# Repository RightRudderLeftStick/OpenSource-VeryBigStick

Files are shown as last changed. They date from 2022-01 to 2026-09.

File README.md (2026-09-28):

# OPEN SOURCE VERY BIG STICK PROJECT 2026
A very large joystick gimbal for very big sticks and now pedals too!

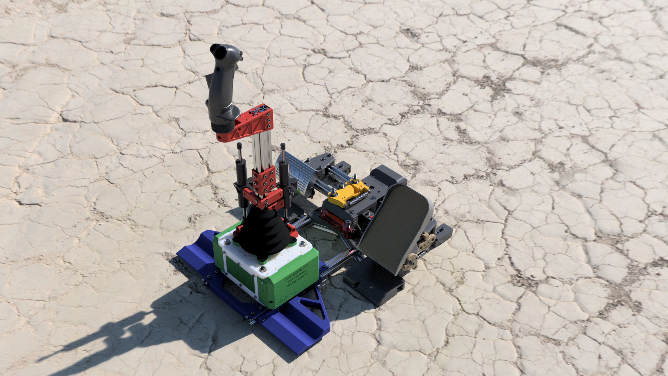
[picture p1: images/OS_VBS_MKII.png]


This totally open source gimbal is designed for end users to either connect existing Thrustmaster compatible grips or attach any custom grip directly to the base. It supports very high spring forces allowing for very realistic feeling flight controls.

It is recommended all parts are printed in PETG, while PLA+ may be acceptable for all parts other than the CAMS, which can be ordered from 3D printed providers in very durable materials.

Checkout the PDF file in the repo to see the bill of materials and the print orientation guide. 

## The current version is Beta 1.4.0

For printing CAMs, it is recommended for "jet" style flying with a full length extension (office chair height) to use "HARD_CAMS" and for medium length (seated low in a sim pit) to use "MED_CAMS". The use of "SOFT_CAMS" is only recommended for warbirds (WWII prop aircraft) or helicopters.

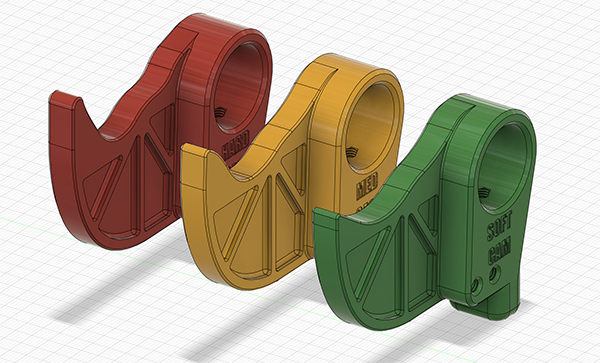
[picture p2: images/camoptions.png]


Check out this build guide below to learn how to assemble the base gimbal!

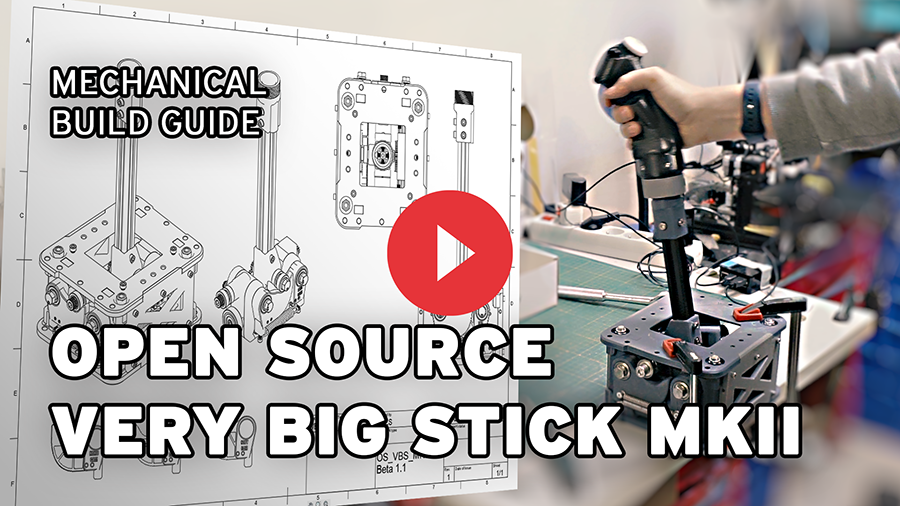
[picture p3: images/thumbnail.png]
Watch the video (https://www.youtube.com/watch?v=IdYbF5dOYag)


This video shows on to connect the electrical wiring and assemble the office chair mount.

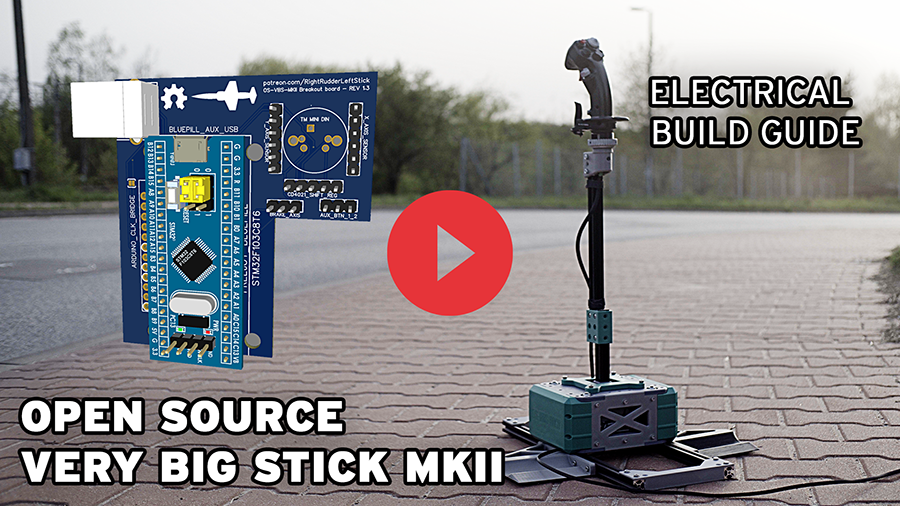
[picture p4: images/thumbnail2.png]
Watch the video (https://youtu.be/jo0v6YuI9vU)


## Patreon
Follow the progress at my patreon. Subscribers recieve early indevelopment F3D project files and other exclusive updates:

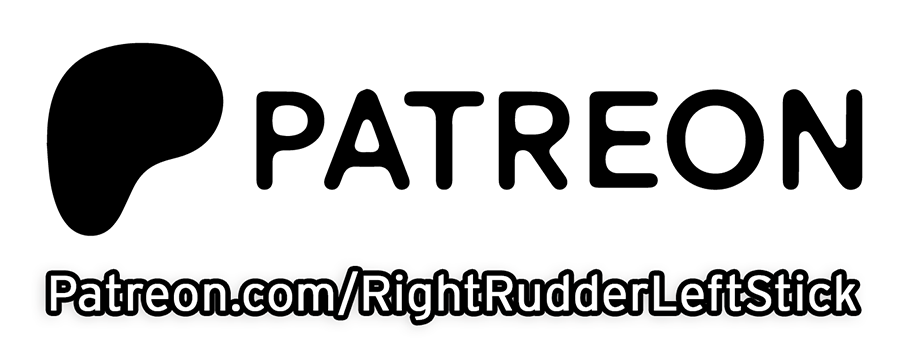
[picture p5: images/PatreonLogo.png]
Link to patreon (https://www.patreon.com/RightRudderLeftStick)


## PCBWAY

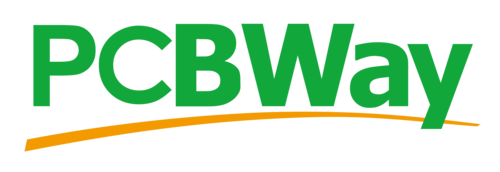
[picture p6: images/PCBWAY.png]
(https://pcbway.com/g/jks8J3)


You can also order the breakout PCB directly from PCBWAY, as well as the CAMs to print in Glass fibre Nylon for extra durability and higher quality than what can be done on most home printers.

### ORDER LINKS FOR PCBWAY
[PCB boards](https://www.pcbway.com/project/shareproject/Open_Source_Very_Large_Stick_Freejoy_MMjoy2_breakout_board_f66f472f.html)

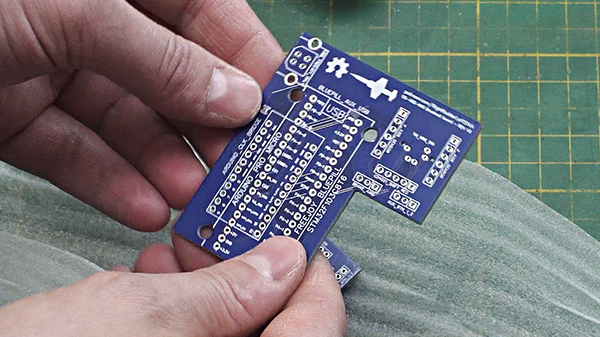
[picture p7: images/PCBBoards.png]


**CAMS** 
(4 are required for a complete set. Order in Glass Fibre Nylon)

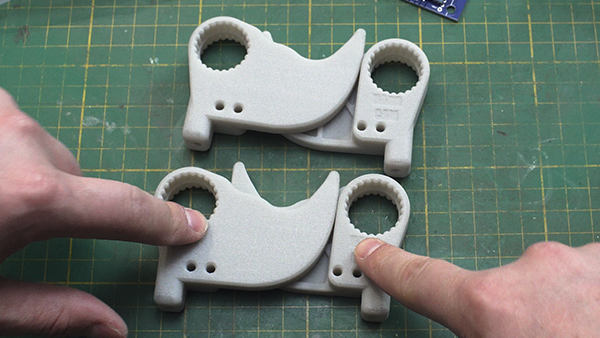
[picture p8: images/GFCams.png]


[Soft Cam](https://www.pcbway.com/project/shareproject/Open_Source_Very_Large_Stick_SOFT_CAM_c2835ecf.html)

[Medium Cam](https://www.pcbway.com/project/shareproject/Open_Source_Very_Large_Stick_MEDIUM_CAM_0f6965ab.html)

[Hard Cam](https://www.pcbway.com/project/shareproject/Open_Source_Very_Large_Stick_HARD_CAM_c53480e9.html)

## Partner Projects

### TheSimNet

Please Checkout TheSimNet's Youtube Channel. He releases designs of fully 3D printable flight grips with TM compatbility. All the renders of the OS-VBS-MK2 use his Free B-8 Grip models for reference. He also sells really cool projects like a very accurate F-15C grip. 

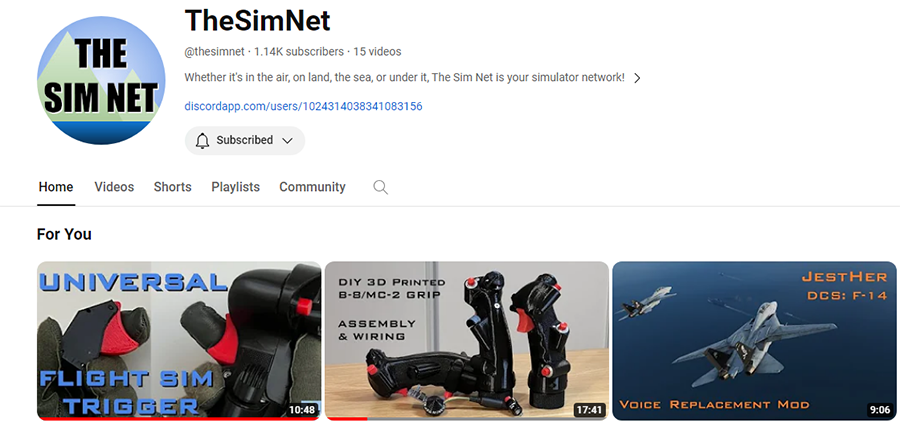
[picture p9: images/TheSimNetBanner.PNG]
Check out this channel (https://youtu.be/-zjJm-5tHko)


### Freejoy

Freejoy is an excellent open source alternative to MMjoy2 and is great for creating for really low cost and powerful USB game controller devices.... if you can still find genuine STM32 boards. 

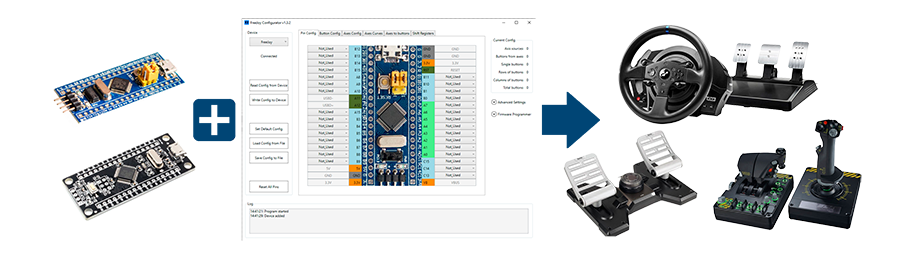
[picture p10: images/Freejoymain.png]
Check out this channel (https://github.com/FreeJoy-Team/FreeJoy)


Link to Freejoy [github.](https://github.com/FreeJoy-Team/FreeJoy)

# Changelog

### 1.4.2
- Added a version 2 of the AS5600 burner script

### 1.4.1
- Pedal stl  & step files now included!

### 1.4.0
- Added A5600 sensor support to the gimbal. New file called *AS5600_Sensor_Mount_vr3.stl* added which can hold the white breakout board sensor.
- Revised the parts *MainSleeve.stl, PitchFrame_PillowBlock.stl, RollFrame_PitchPin_Gear.stl, RollFrame_CamSide.stl & RollFrame_GearSide.stl* to update to the compliance holes from the pedal design
- *RollFrame_PitchPin_Gear.stl* now prints standing up for better support of the magnet slot.
- *PitchFrame_TopPlate.stl* has been revised with the latest patreon info and version code.
- Note the Analog pins on the AS5600 sensor should always be aligned to face the N on the magnet slot. This centers the 245 and 290 degree range thats burn with the script.
- *OuterCamCover_Solid.stl* updated with CLOS tier patreon backer credits.

### 1.3.8
- Added STM32 script for burning AS5600 sensor.

### 1.3.7
- Changed all the *.3mf files to *.stl files as there is an incompatbility with the 3mf generated by cura with orca/bambu slicer.

### 1.3.6
- Added a TPU_Boot.3mf which is a printable TPU cover to go over the top of the gimbal to keep dust and debris out of the mechanism. Print slowly as there are 60 degree overhangs in the design.

### 1.3.5
- Added the OuterCamCover_FreejoyUSB.3mf which has a port for the USB-B port when using freejoy to stick out. a regular USB cable connected directly to the bluepill or ardiuno can also go through this hole with a strain relief plate attached with M3 screws

### 1.3.4
- Added the sideplate.3mf. These just snap over the sides of the gimbal that are open to cover them.
- Added the authentikit Spade grip adapter, see community add-ons directory.
- Modified the wheel chocks and crossbar pieces to have 1.5mm of height from the floor. This raises the aluminum extrusions so the edges don't scratch hardwood floors. This also will be for heigh compatiblity with the rudder pedals which will also have the 1.5mm of space.

### 1.3.3
- Added the bushplane grip as an optional single button handle for the gimbal. included in the BushPlane_Grip directory.
- Added a new restrictor plate called "CYC_Split_RestrictorPlate_20degrees.3mf" that replaces the original 3mf of the restrictor plate. It comes in two parts and allows itself to be removed or replaced without diassembling the stick column

### 1.3.2a

- Fixed a net error in the PCBbreakout board (now revision 1.5) which required reordering the IO buttons on the breakout.

### 1.3.2

- Fixed an error in the breakout board where the TM mini DIN had the wrong pin orientation. 
- Fixed mislabelling on the USB breakout pins.
- Added 13 extra button IO pins to the breakout board. Now using freejoy a B-8 style grip can have all the buttons wired directly without using a shift register.

### 1.3.1

- Fixed the quantity in the build guide for "2020_Crossbar.3mf" from 1 to 2.

### 1.3

- Updated with electrical gerber files for the breakout board
- New TM adapter piece that has an offset for use with common chairs
- Revisions to several pieces, including a new "PitchFrame_TopPlate" that includes extra M5 holes for the future cyclic piston damper upgrade and cut outs to make it easier to fit a socket wrench into the gimbal to change cams
- Added Add-on for office chair mount
- Added the configuration file for MMJOY2
- Adjusted the PitchFrame_PillowBlock.3mf to have wider holes for feeding the wires through.
- Redesigned the CAMs to not require the Cam_Bearing_washer.3mf and to nicely friction fit the 608 bearings with compliance holes.

### 1.2
- Revised the TM adapter piece to have the clearance for the X shape at the bottom of the TM grip connector

### 1.1

- Fix to the TM adapter to add a second set of holes.

### 1.0

- Intial release of the mechanical parts of the gimbal, as seen in the mechanical guide video.

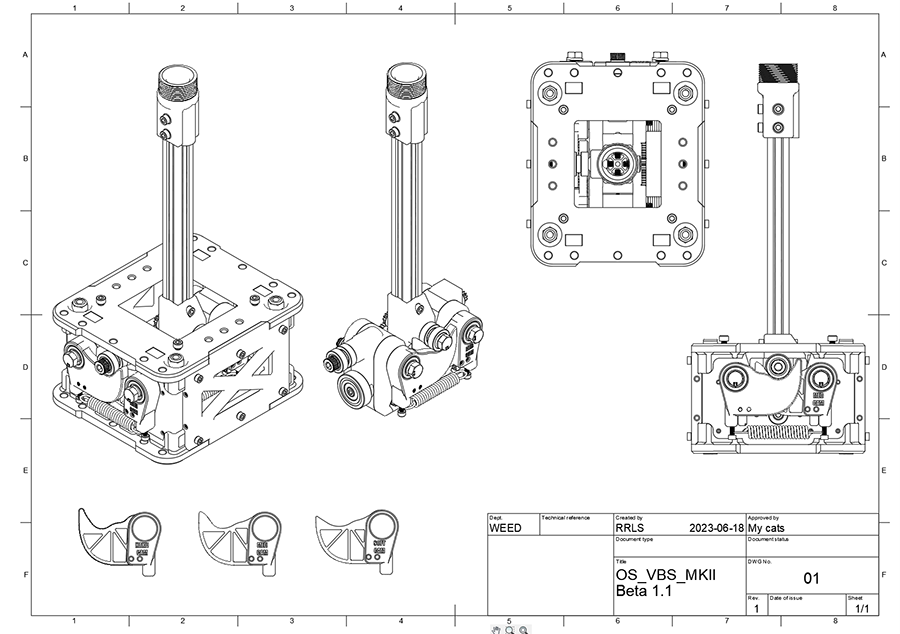
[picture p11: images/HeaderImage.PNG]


---



[This project is licensed as CC BY-SA 2.0](https://creativecommons.org/licenses/by-sa/2.0/)

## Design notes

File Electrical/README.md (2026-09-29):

# Firmware for microcontrollers

## Breakout Board

The breakout board is designed to socket either a STM32F103C8 microcontroller board (freejoy) or an Arduino Pro Micro (MMJOY2 or custom code). You can use the gerber file to order the PCB from your local assembler, or order directly from PCBWAY [here](https://www.pcbway.com/project/shareproject/Open_Source_Very_Large_Stick_Freejoy_MMjoy2_breakout_board_f66f472f.html).

Current Revision is 1.5

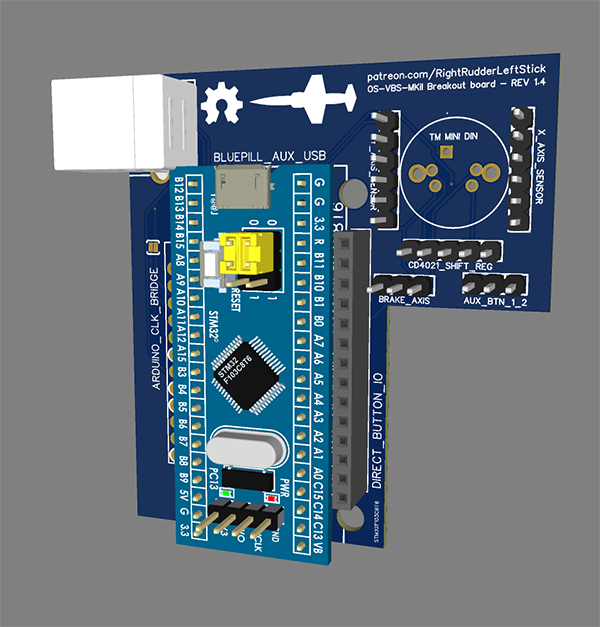
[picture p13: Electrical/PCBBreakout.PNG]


## MMJOY2 version

The MMJOY2 variation will require an Andruino Pro Micro, and the solder bridge must be connected on the PCB to set it for this configuration.

This is the public directory of all the version of MMJOY2 that were released before the project was halted.

Link to [website.](https://sites.google.com/site/mmjoyproject/%D1%84%D0%B0%D0%B9%D0%BB%D1%8B-%D0%B4%D0%BB%D1%8F-%D1%81%D0%BA%D0%B0%D1%87%D0%B8%D0%B2%D0%B0%D0%BD%D0%B8%D1%8F) 

For best reliabilty and compatibility with the included .mmjoy2 file. Use MMJOY2[v20160818upd1].rar

## Freejoy version

Using the freejoy version requires a **genuine** STM32F103C8 microcontroller board. Counterfeit STM32 chips cause all sorts of unpredictable problems with the Freejoy firmware. Try and order your STM32F103C8 from a trusted retailer with a proper return policy. 

Freejoy version requires a specialized firmware on top of v1.7.1_1b3 that is publically avaliable. Due to the length of the stick and wiring the timing of the CD4021 shift registers causes ghosting of inputs. This specialized firmware adjusts this. It is in the /Firmware/ directory.

In the /config/ directory there is also the w.i.p config file. It doesn't yet support the new IO pins of the 1.4 board revision.

Link to Freejoy [github.](https://github.com/FreeJoy-Team/FreeJoy)

## AS5600 Sensor Option

Because of supply chain issues, the EOL of the TLE5011 sensor, tariffs, some regions not having aliexpress, I've decided to support the very common AS5600 encoder sensor on the white breakout board. 

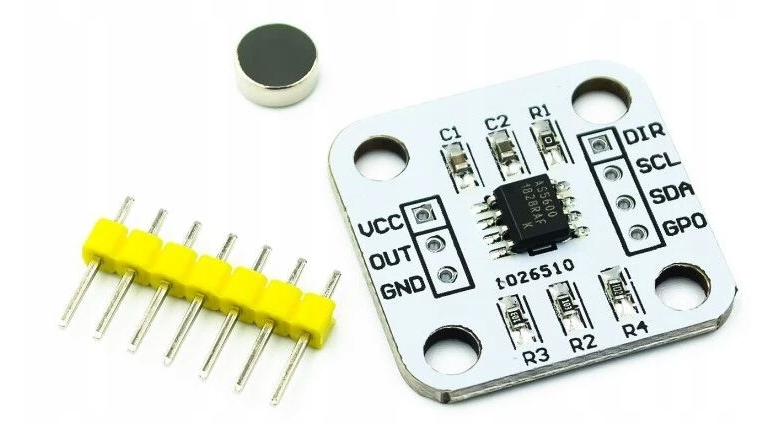
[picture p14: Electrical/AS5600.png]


The AS5600 is extremely common, as its used as an encoder on motors. The problem is its range is a full 360 degrees, which means for the 37 degrees we actually use that's only 440 steps of sensitivity over the range, which is reduced even more if you have a noisy signal.

I've created a script that can run on the bluepill before flashing freejoy that uses the internal chip register to instead convert the 360 range to a much narrower 50 degrees. This is a permanent "burn" operation into the chips memory. What it does is take the 360 degree range and truncate it to 245 - 290 degrees, which now will respond with 0-3.3v over the analog out, massively improving the sensors sensitivity. What this means is mounting the small magnet is extremely important to get within 10 degrees of north orientation, as we have 50 degrees to fit the 37 degrees of actual axis movement.

Here is the pin out guide to setting up the ship programmer.

BLUEPILL | 3.3v | GND | B6 | B7 | 
--- | --- | --- | --- | --- |
AS5600  | VCC | GND | SCL | SDA |

You load the [STM32_AS5600_Burner.bin](https://github.com/RightRudderLeftStick/OpenSource-VeryBigStick/tree/main/Electrical/As5600%20Sensor) with the ST-link utility just like how you flash the freejoy firmware for the first time. 

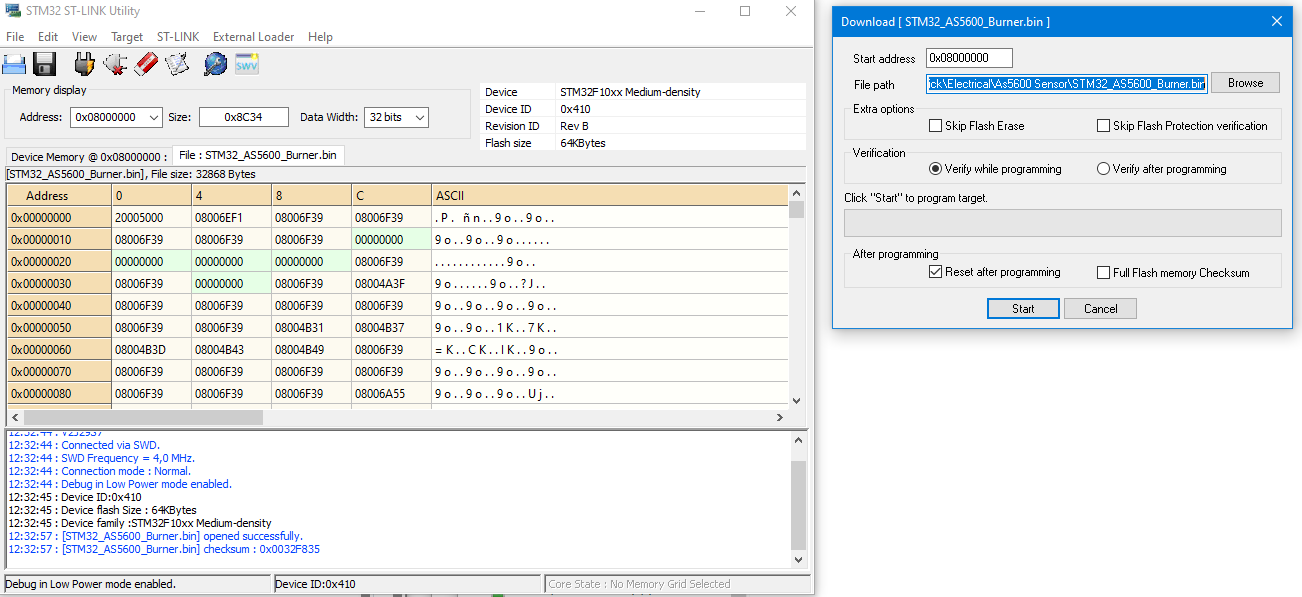
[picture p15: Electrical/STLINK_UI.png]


Then while the board is powered from the ST-link v2 and connected to the AS5600 board, take a wire connected to the A1 pin on the bluepill and touch it to the extra GND pin on the bluepill. The LED on the board should flash 3 times and the 0-360 degree range of the sensor is now permamently burned to 245-295 degrees. So now over these 50 degrees the analog pins will output 0-3.3v range.

Now you use the analog pins of the AS5600 as you would a pot or other hall effect sensor.

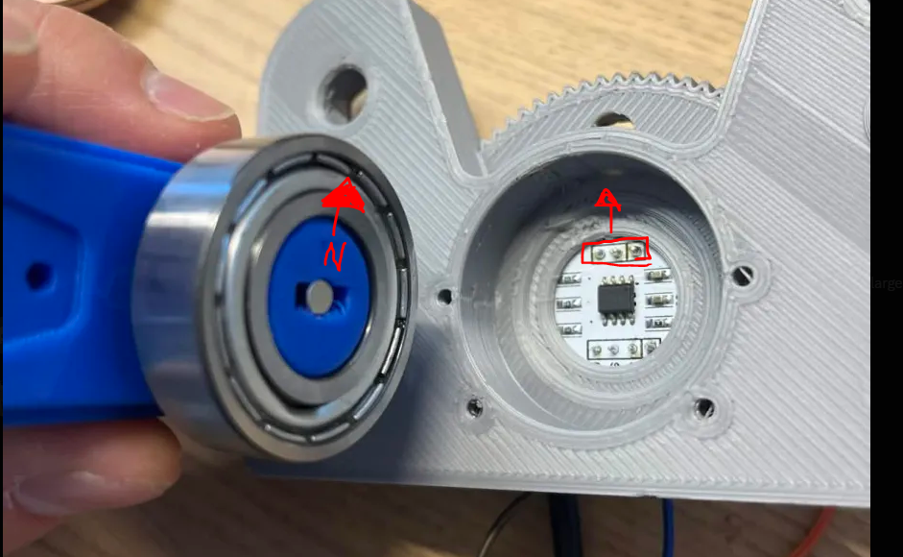
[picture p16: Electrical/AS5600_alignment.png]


When you place the AS5600 white breakout board into the holder, align the 3 analog pins in the same direction as the North of the magnet as pictured here. In the gimbal and the pedals is different, as the magnet holder slot is at different orientations for printablity. 

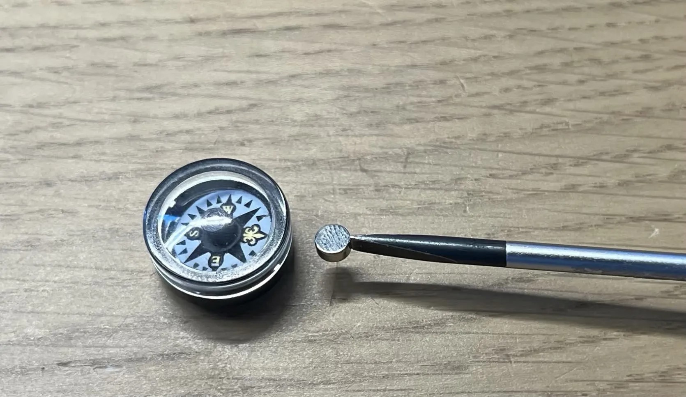
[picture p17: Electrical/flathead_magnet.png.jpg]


Note that this mechanism only allows around 37 degrees of moment, which means the small magnet can have only 13 degrees of misalignment. Use the edge of a very fine flat screwdriver to align the north pole directly with the N printed on the pin. Use a compass to verify that it is in fact the north pole. Test the axis before fully assembling to make sure you are not hitting the edge of the range during normal movement. If you get the N and S poles flipped, you can also rotate the white board 180 degrees in the mount.

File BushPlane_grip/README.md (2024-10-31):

# Bushplane add-on

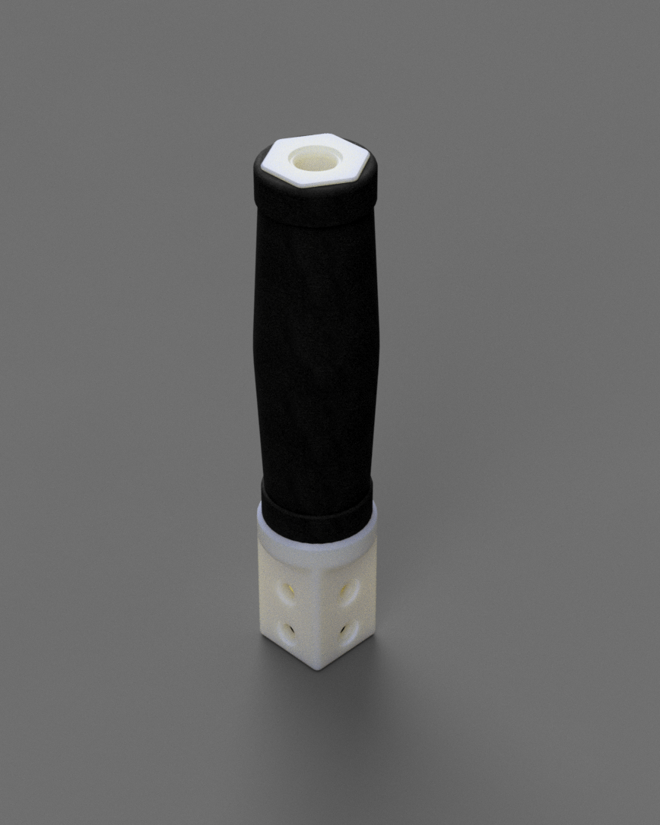
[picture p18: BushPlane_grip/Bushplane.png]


## Basic grip

This add-on is a very basic “bushplane” style grip for the gimbal. This simulates a single button grip used in small aircraft and gliders.

It uses a single common 12mm push button.

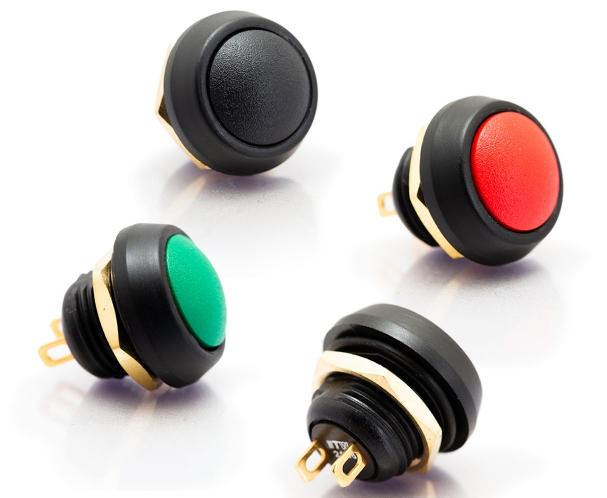
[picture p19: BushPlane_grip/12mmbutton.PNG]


Wiring requires using the extra IO pins on the PCB (AUX_BTN_1_2) and the exact wiring differs with freejoy builds (which is BTN1 and GND) or arduino micro (BTN1 and BTN2)

The foam grip is a standard 34x125mm long EVA foam bicycle grip. The cap on the top threads on with printed threads.

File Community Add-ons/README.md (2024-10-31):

# Community add-ons or modified parts 

Here is a directory to community submitted add-ons or modifications of the base parts

## McDinggle

### TM_Adapter_short.stl & VKB_Adapter.stl

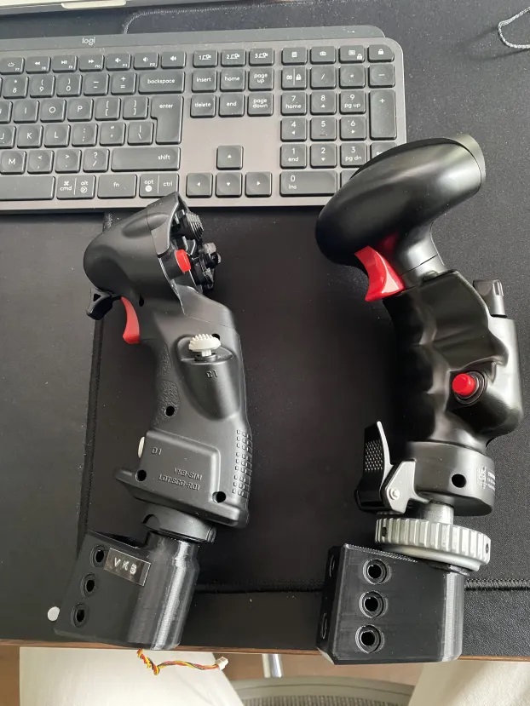
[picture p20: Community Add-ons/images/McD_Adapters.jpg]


McDinggle has contributed these modifed parts, first a TM adapter that has less threads to shorten the overall length of the adapter and a modified adapter for attaching a NXT Gladiator grip. 
The method for reading inputs from the VKB is still being researched.

## Authentikit

### Spitfire spadegrip adapter

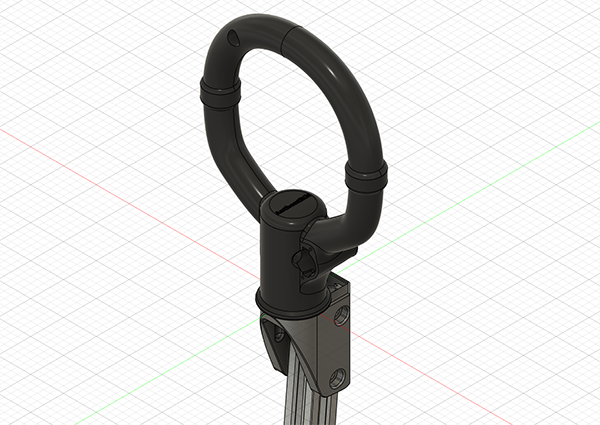
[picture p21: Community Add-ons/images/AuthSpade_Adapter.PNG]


Using the excellent https://authentikit.org/ 3d printable flight controls, you can print the upper piece of the Spitfire MkIX spade grip https://download.authentikit.org/filebase/index.php?file/3-spitfire-mkix-starter-kit-a/ and attach it to the 2020 aluminum extrusion directly. The grip is tilted 5 degrees forward to emulate the real "center" angle of the spadegrip. 

For connecting the buttons and brake axis, it is recommended to use the freejoy configuration and connect to the added IO pins (DIRECT_BUTTON_IO).

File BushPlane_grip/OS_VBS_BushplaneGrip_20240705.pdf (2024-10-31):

https://github.com/RightRudderLeftStick/OpenSource-VeryBigStick Jul 5, 2024

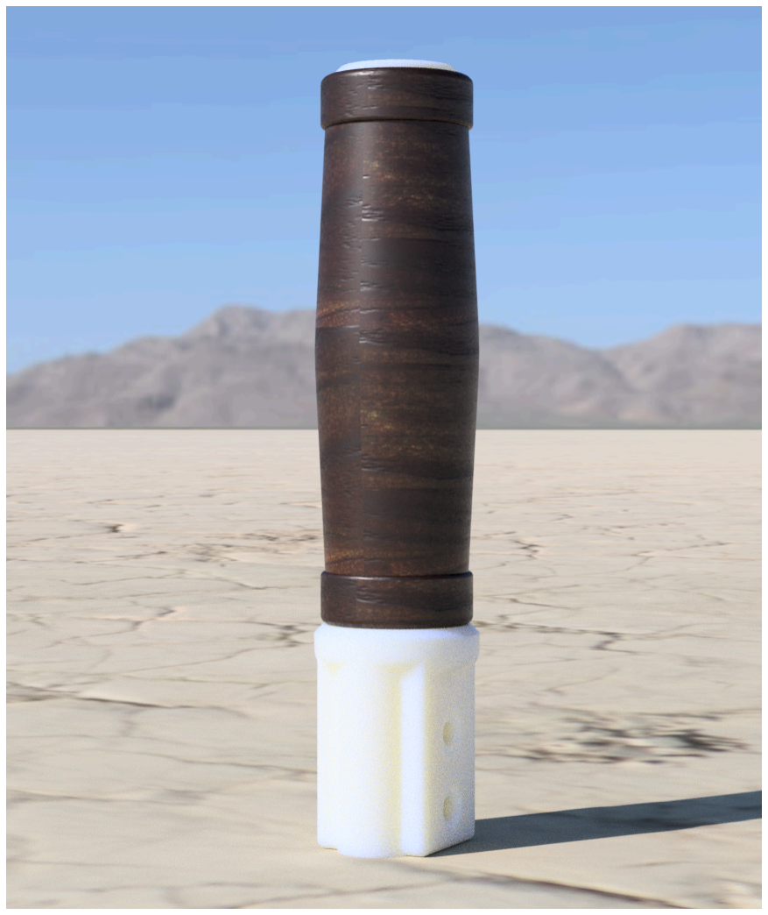
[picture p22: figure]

# Open Source - Very Big Stick MKII

## Bushplane Grip

Release 1.0v

2024-07-05

Support this project at https://www.patreon.com/RightRudderLeftStick

This add-on is a very basic “bushplane” style grip for the gimbal. This simulates a single button grip used in small aircraft and gliders.

It uses a single common 12mm push button.

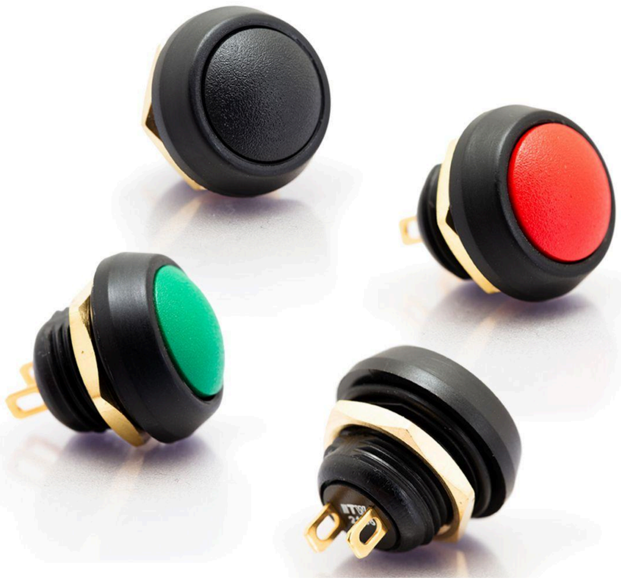
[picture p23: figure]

Wiring requires using the extra IO pins on the PCB (AUX_BTN_1_2) and the exact wiring differs with freejoy builds (which is BTN1 and GND) or arduino micro (BTN1 and BTN2)

The foam grip is a standard 34 x 125mm long EVA foam bicycle grip. The cap on the top threads on with printed threads.

## 3mf Part Reference

Here is information on each 3mf file included with the build and a reference image showing the correct print orientation.

### BushPlane_2020_Grip_Base.3mf

Quantity: 1 (consider using raft for stability)

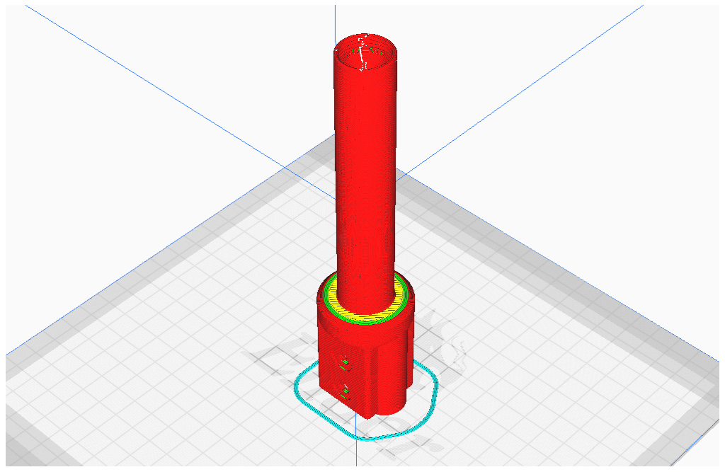
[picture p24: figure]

### BushPlane_12mm_ButtonCap.3mf

Quantity: 1

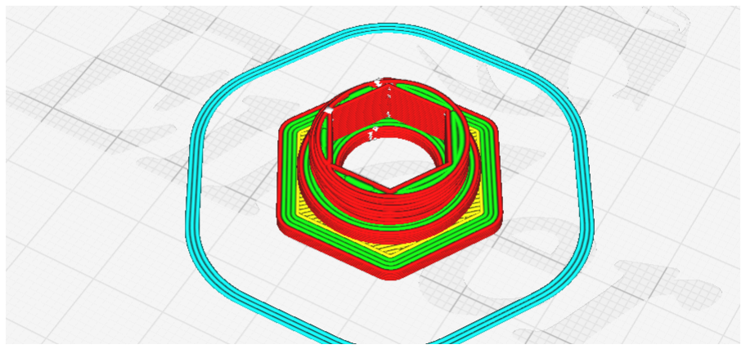
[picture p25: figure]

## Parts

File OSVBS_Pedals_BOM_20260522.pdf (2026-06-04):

## LIST CREATION DATE 2026-05-22

# 01 PRIMARY PEDALS

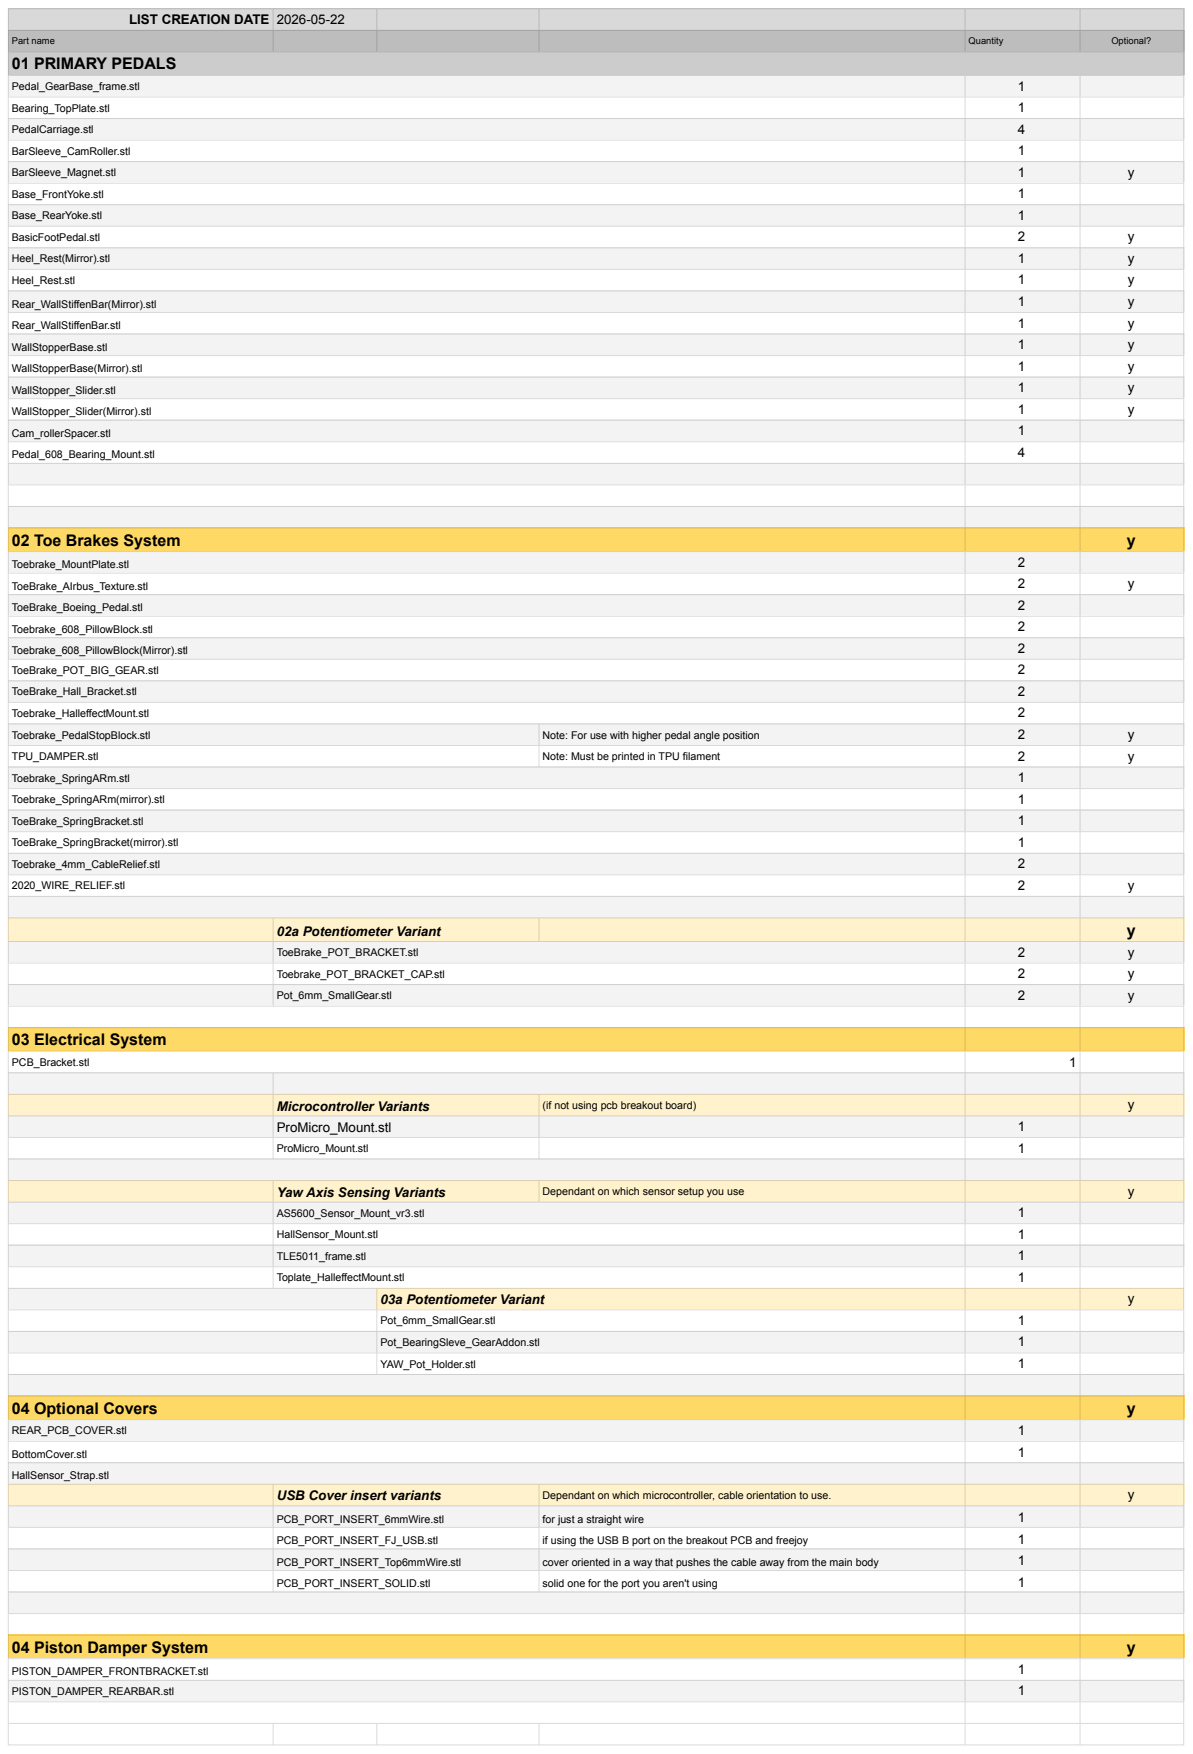
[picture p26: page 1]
Part name; Quantity; Optional?; Pedal_GearBase_frame.stl; Bearing_TopPlate.stl; PedalCarriage.stl; BarSleeve_CamRoller.stl; BarSleeve_Magnet.stl; Base_FrontYoke.stl; Base_RearYoke.stl; BasicFootPedal.stl; Heel_Rest(Mirror).stl; Heel_Rest.stl; Rear_WallStiffenBar(Mirror).stl; Rear_WallStiffenBar.stl; WallStopperBase.stl; WallStopperBase(Mirror).stl; WallStopper_Slider.stl; WallStopper_Slider(Mirror).stl; Cam_rollerSpacer.stl; Pedal_608_Bearing_Mount.stl; 02 Toe Brakes System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

LIST CREATION DATE | 2026-05-22
Part name | | Quantity | Optional?
PRIMARY HARDWARE | | Notes
1KG Spool PETG 1.75mm filament | 2 | PLA+ untested. Do not print the CAMs in PLA as they will distort over time. if using PET-CF make sure you get good layer adhesion
50g TPU filament | 1 | If you are using the optional TPU_DAMPER.stl for the toe brakes.
2020 extrusion 40cm lengths | 4 | One of them may be optionally cut in half for the heel rests or used straight
M8x100 bolt | 2 | prefer hex head as they use a nylock nut and are easier to drive in with a socket wrench.
M8x60 socket head bolt | 4 | Must be socket head, they recess into the part at the head and cannot work with hex head.
M8x35 socket head bolt | 9 | You can also use hex head screws for these
m8 nuts | 10 | get standard sizes, many of these are dropped into parts as internal threads and thus have to be nominal ISO sized. (~6mm thick, ~15mm widest corner to corner)
m8 nylock lock nuts | 6 | get standard sizes, many of these are dropped into recesses and thus have to be nominal ISO sized. Not thinner than standard (~8mm thick, ~15mm widest corner to corner)
m8 washer | 6
m8 spring washer | 2
m6x25 socket head bolt | 4 | Must be socket head, they recess into the part at the head and cannot work with hex head.
m6 nylock lock nuts or flange nuts | 4 | You can use flange nuts instead of nylock nuts if the m6x25 doesn't have enough thread to bite the nylon part of the nut
M5x50 Socket Head bolt | 10
M5x20 Socket Head bolt | 30
M5x20 COUNTERSUNK bolt | 6 | Countersunk, so angled top, measured from top face to end of threads 20mm.
M5x16 Socket Head bolt | 28
M5x8 Socket Head bolt | 17
M5 nuts | 43 | get standard sizes, many of these are dropped into parts as internal threads and thus have to be nominal ISO sized. (~4mm thick, ~9mm widest corner to corner)
M5 t slot drop in nuts | 39 | Get the kind that drops in as its easier than having to slide them in one after enough and forgetting one.
m5 washer | 4
m4x20 socket head bolt | 4
m4x16 socket head bolt | 16 | Must be socket head, they recess into the part at the head and cannot work with hex head.
m4 nuts | 6
m3x12 bolt | 9 | 9th one is optional if using the potentiometer option for the gear teeth mount.
m3x6 bolt | 10
608 skateboard bearings | 20 | Get good ones. Buy in a 20 pack.
6003 bearings | 2 | same big bearings from the main gimbal.
Extension spring with loop ends. ~55mm unloaded | 4 | two for the cams on the main pedal, one for each toe brake. On the cams you might use just 1 spring for less force.
FRT-C2-301-G1 Rotary damper | these can now be a bit tough to come by due to tariffs and other stupidity, these are made obsolete if you have the motorcycle steering damper installed. | y
DAMPER ADD-ON | Notes
M8x40 socket head bolt | 1 | Socket head, this one is shorter so it doesn't hit at the back
M8x50 socket head bolt | 1 | Spocket head
M8 nylock lock nuts | 2 | This needs to by a nylon locking nut so you can tignten the grip but the damper can still swing naturally.
Steering damper | 1 | Get a quality one, check if for "stiction" after getting it and return if bad, you'll get annoyed quick if its sticky or squeaks
ELECTRICAL | Notes
B10K 10K Ohm Potentiometer 3Pin 15mm | 3 | This is if you want to make the pedals with simple pots and gear driven, recommended for first timers but you'll want to upgrade to hall effect later on | y
A1324LUA-T Hall Effect Sensor | 3 | This is for hall effect sensor option and is recommended. Get quality ones not the cheaper SS49E sensor which has bad noise at 3.3v with freejoy.
1 meter 3 strand flexible wire | 1 | This is what runs to each pedal for the toe brakes, so something that can handle lots of flexing over time.
8x3mm neodymium magnets | 5 | You need two per toe brake and one for the main pedals if not using the potentiometer config. Fridge magnet type with north/south of the flat faces.
AS5600 sensor and breakout board | 1 | This is an alternative to the Hall effect sensor for the yaw axis, and is superior if you can burn the range using the extra script.
Arduino Pro Micro | 1 | this is for MMJOY2 based controller | Either Or STM32F103C8 "Bluepill" | 1 | This is for Freejoy based controller. Note that there is a plague of counterfeits, only by from trusted seller.
OSVBS breakout pcb | 1 | This is optional if you've had a set made from the gimbal you will have a spare. It allows use of the USB-B port with freejoy | y

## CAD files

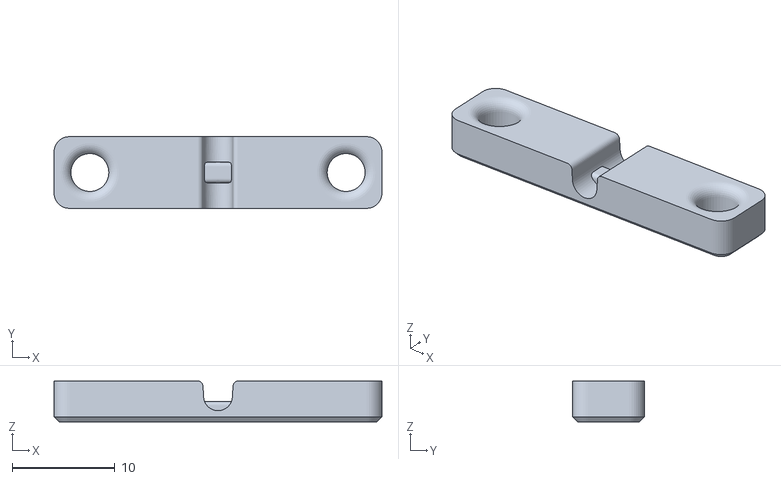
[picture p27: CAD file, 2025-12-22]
Printable Models/Optional Add-ons/ASSY_USBCABLE_STRAIN_RELIEF.stl
32.0 x 7.00 x 4.00

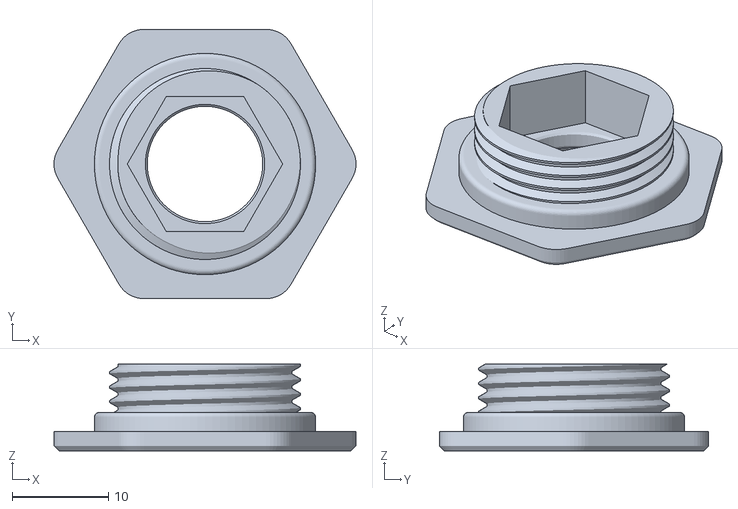
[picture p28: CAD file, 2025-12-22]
BushPlane_grip/BushPlane_12mm_ButtonCap.stl
31.4 x 28.0 x 9.00

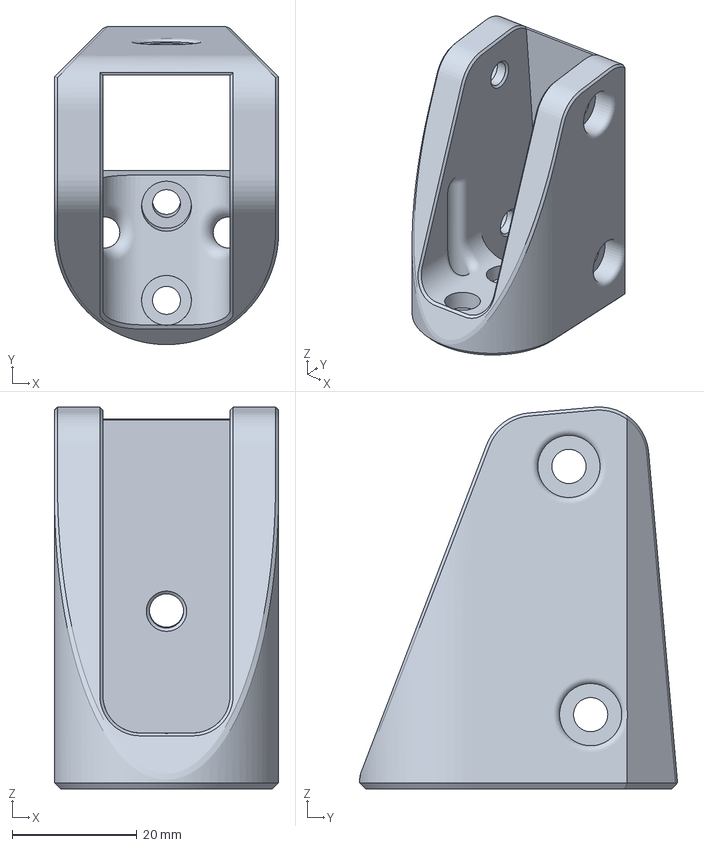
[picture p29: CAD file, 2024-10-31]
Community Add-ons/SpitfireSpade_MountBracket.3mf
36.0 x 51.1 x 61.3 mm

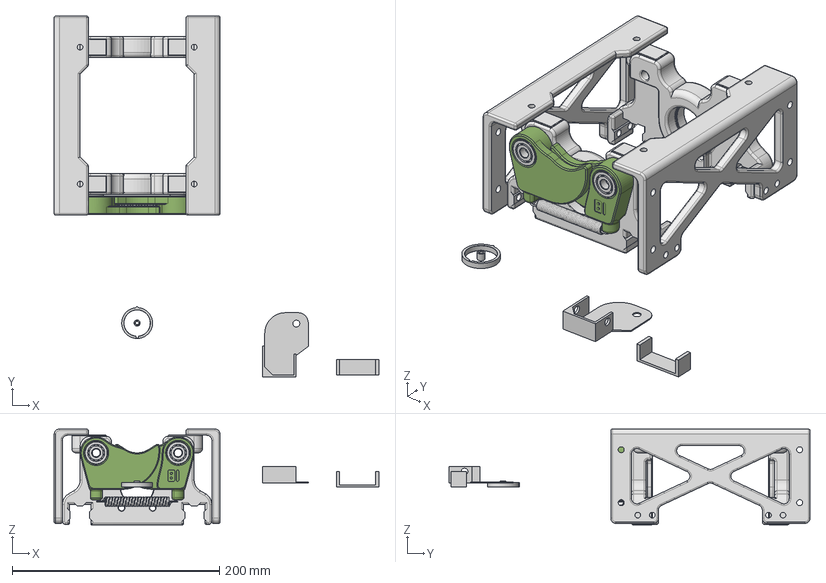
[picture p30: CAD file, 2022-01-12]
Object 77-B BIG v34_2022-1-11.step
313.0 x 348.0 x 92.5 mm
BASE_ROLL_CAMS x 2
Cam (hard center) 2 x 2
9044K265_Music-Wire Steel Extension Spring
5972K91_Ball Bearing x 4
Cam_bearing_washer x 2
98689A116_General Purpose 18-8 Stainless Steel Washer x 2
Sidewall x 2

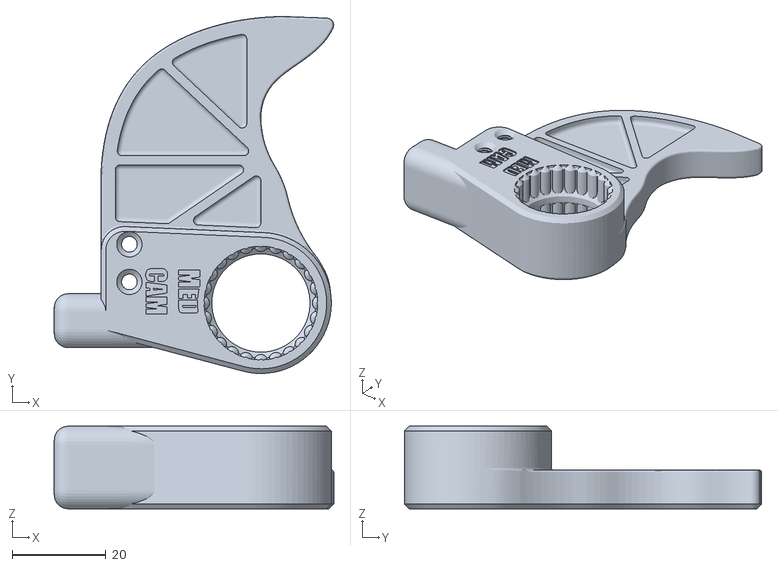
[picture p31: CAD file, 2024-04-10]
Printable Models/Cam Profiles/MED_CAM.stl
59.5 x 76.0 x 17.6

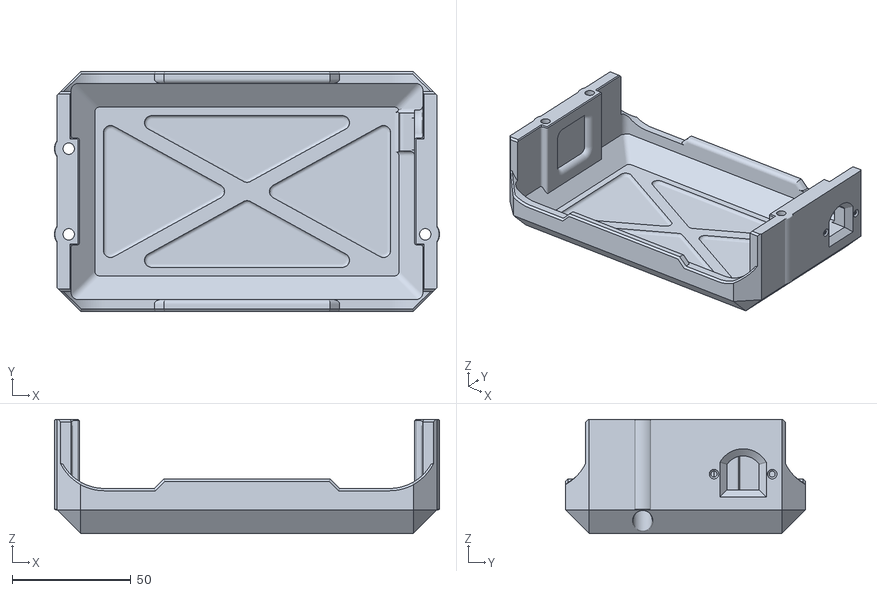
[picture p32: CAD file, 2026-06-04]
Printable Models/Optional Add-ons/OuterCamCover_Solid.stl
162.0 x 101.0 x 48.0

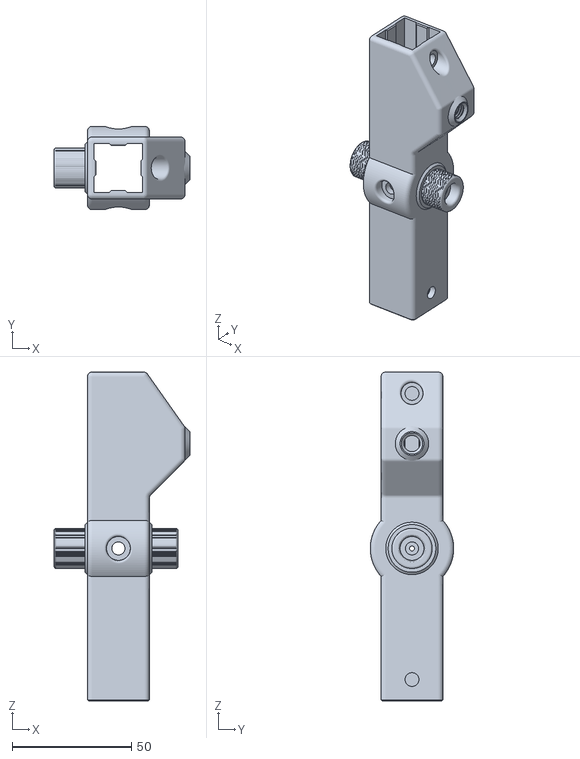
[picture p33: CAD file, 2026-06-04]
Printable Models/Rudder_Pedals/01_Primary Pedals/BarSleeve_CamRoller.stl
57.0 x 35.0 x 138.0

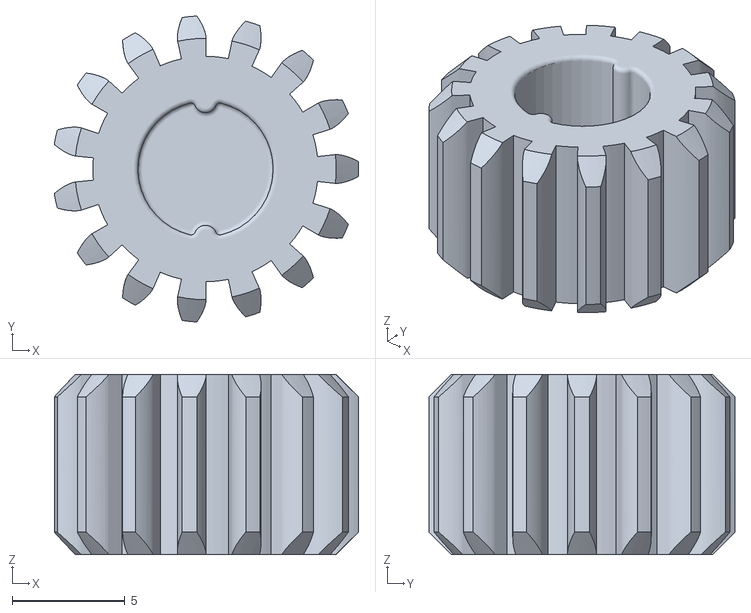
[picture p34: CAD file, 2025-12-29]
Printable Models/Rudder_Pedals/02_Toe Brakes System/Potentiometer Variant/Pot_6mm_SmallGear.stl
13.5 x 13.6 x 8.00

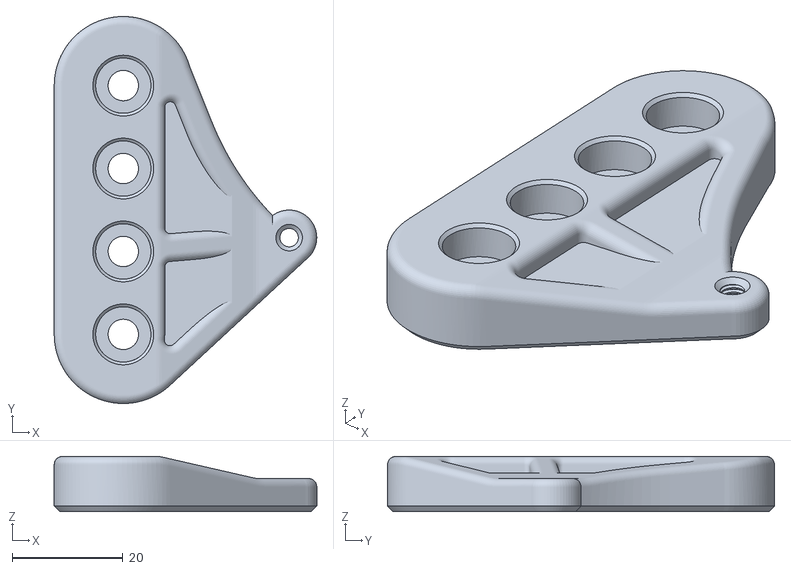
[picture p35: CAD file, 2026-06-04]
Printable Models/Rudder_Pedals/02_Toe Brakes System/ToeBrake_SpringBracket(mirror).stl
47.5 x 70.0 x 10.0

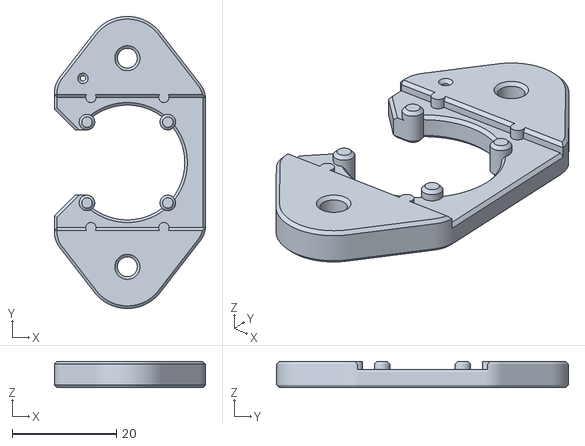
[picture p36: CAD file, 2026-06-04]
Printable Models/Rudder_Pedals/03_Electrical System/AS5600_Sensor_Mount_vr3.stl
29.0 x 56.0 x 5.00

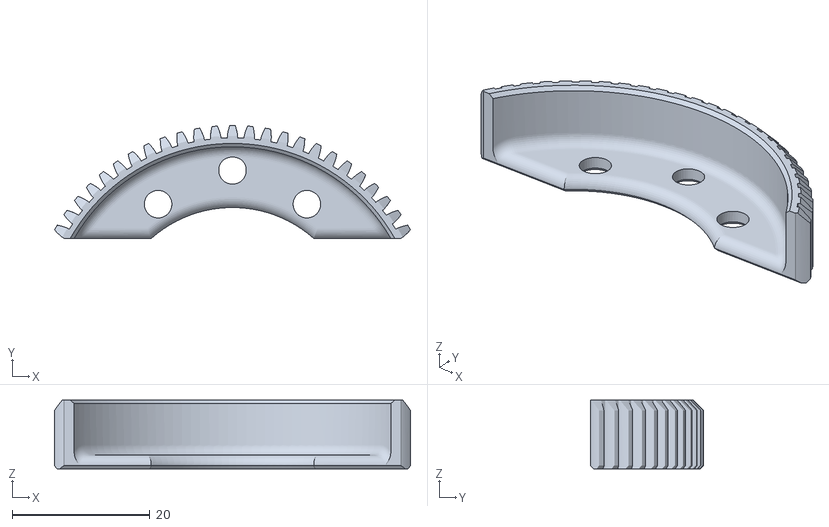
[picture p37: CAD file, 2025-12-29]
Printable Models/Rudder_Pedals/03_Electrical System/Potentiometer Variant/Pot_BearingSleve_GearAddon.stl
51.7 x 16.4 x 10.0

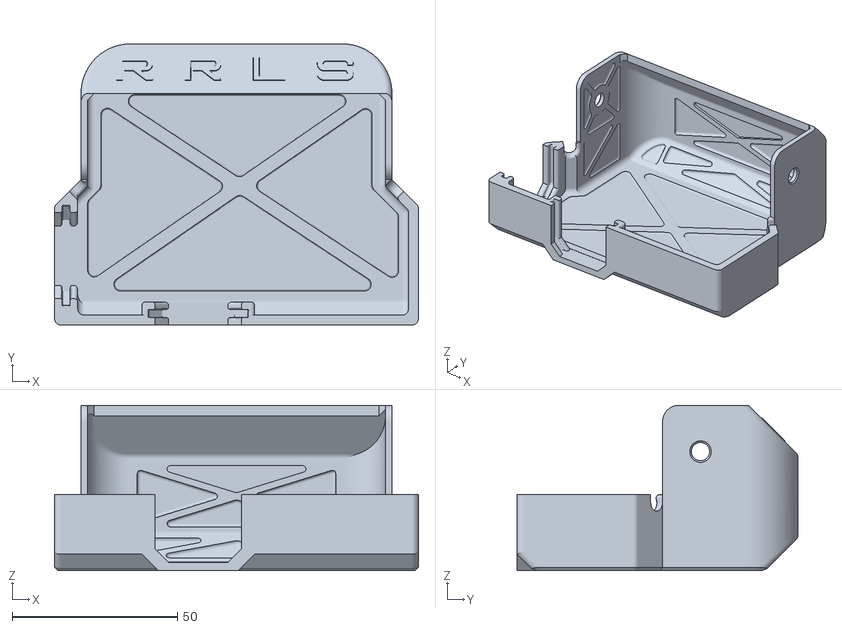
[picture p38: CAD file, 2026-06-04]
Printable Models/Rudder_Pedals/04_Optional Covers/REAR_PCB_COVER.stl
110.0 x 85.0 x 50.0

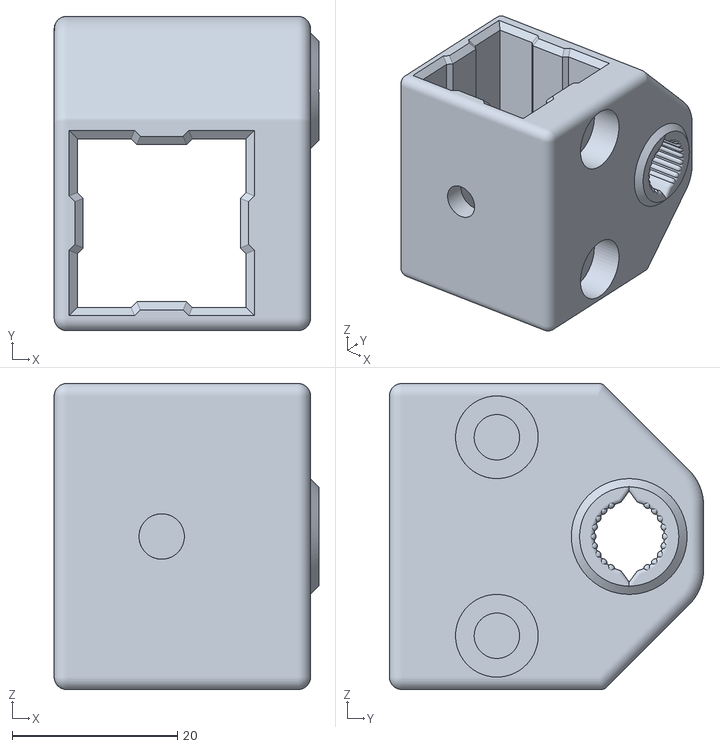
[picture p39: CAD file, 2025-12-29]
Printable Models/Rudder_Pedals/05_Piston Damper System/PISTON_DAMPER_REARBAR.stl
32.0 x 38.0 x 37.0

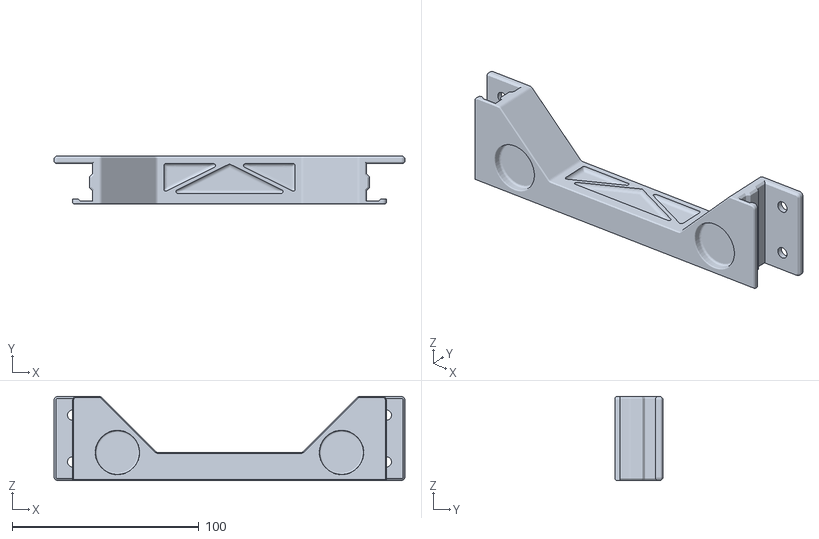
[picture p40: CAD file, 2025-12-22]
Printable Models/Stick_Base/Chair Base Add-on/2020_Crossbar.stl
188.0 x 25.5 x 45.0

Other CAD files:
Printable Models/Stick_Base/PitchFrame_TopPlate.stl
BushPlane_grip/Bushplane_2020_Grip_Base.stl
Community Add-ons/McDinggle_VKB_Adapter.stl
Printable Models/Cam Profiles/HARD CAM.stl
Community Add-ons/McDinggle_TM_Adapter_short.stl
Printable Models/Cam Profiles/SOFT_CAM.stl
Printable Models/Optional Add-ons/2020_CYC_OFFSET.stl
Printable Models/Optional Add-ons/CYC_Split_RestrictorPlate_20degrees.stl
Printable Models/Optional Add-ons/SidePlate_Cover.stl
Printable Models/Optional Add-ons/TPU_BOOT.3mf
Printable Models/Rudder_Pedals/01_Primary Pedals/BarSleeve_Magnet.stl
Printable Models/Rudder_Pedals/01_Primary Pedals/Base_FrontYoke.stl
Printable Models/Rudder_Pedals/01_Primary Pedals/Base_RearYoke.stl
Printable Models/Rudder_Pedals/01_Primary Pedals/BasicFootPedal.stl
Printable Models/Rudder_Pedals/01_Primary Pedals/Bearing_TopPlate.stl
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

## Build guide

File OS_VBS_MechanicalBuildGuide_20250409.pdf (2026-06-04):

https://github.com/RightRudderLeftStick/OpenSource-VeryBigStick Apr 9, 2026

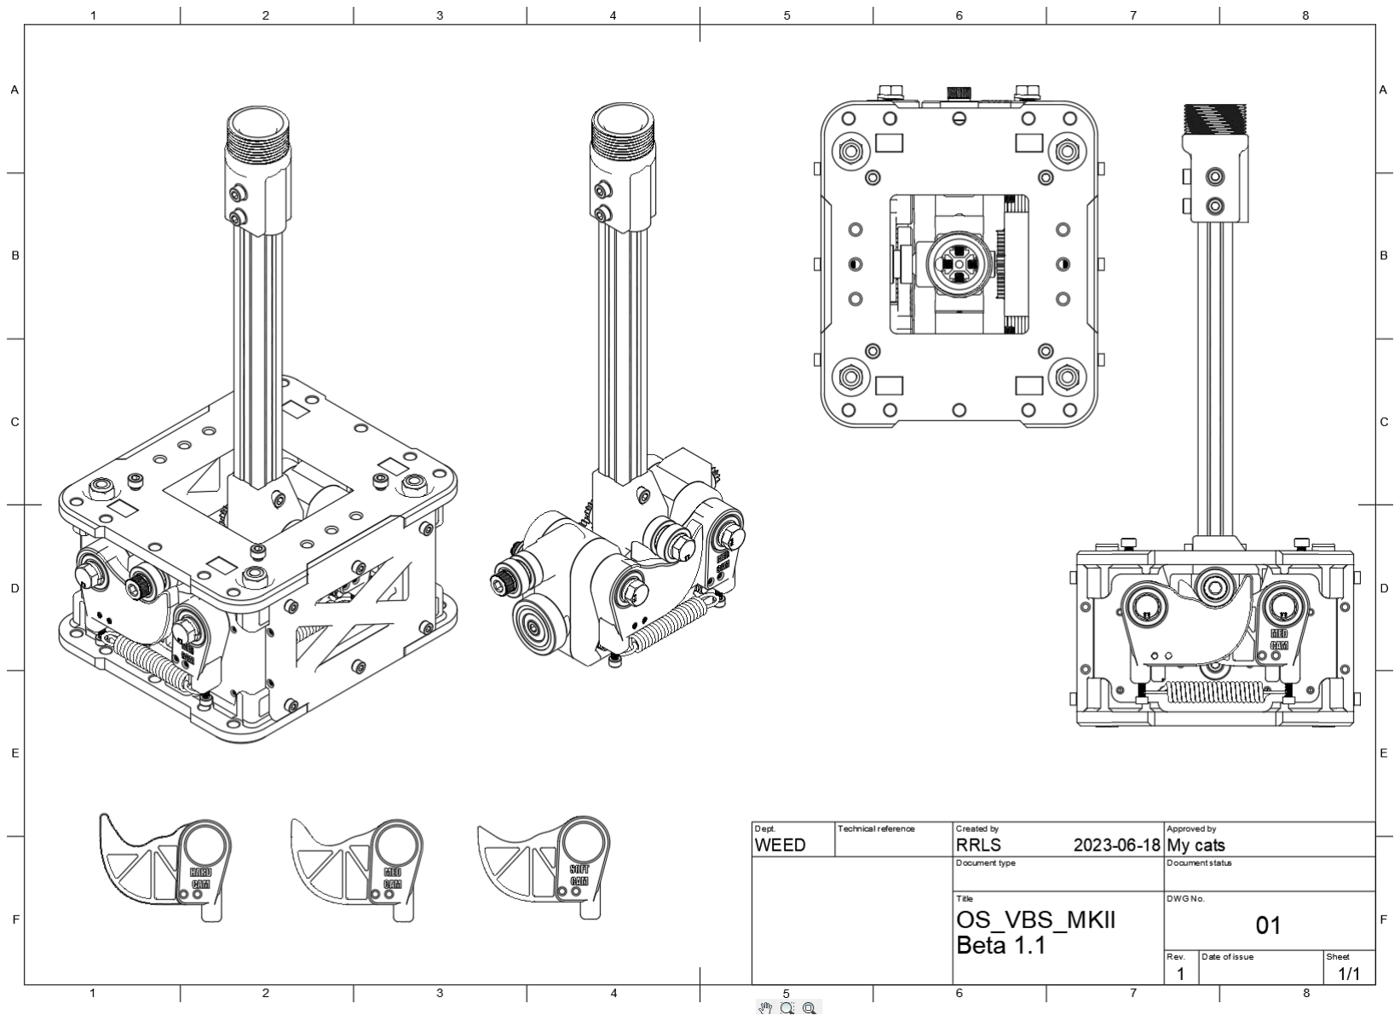
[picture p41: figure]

# Open Source - Very Big Stick MKII

## MECHANICAL BUILD GUIDE

REVISED Beta v1.4.0

2025-04-09

Support this project at https://www.patreon.com/RightRudderLeftStick

## Mechanical Build Guide Video

Instructions on how to assemble the OS_VBS MKII gimbal is available on rightrudder-leftstick’s youtube channel. Please watch and follow carefully on how to assemble these components.

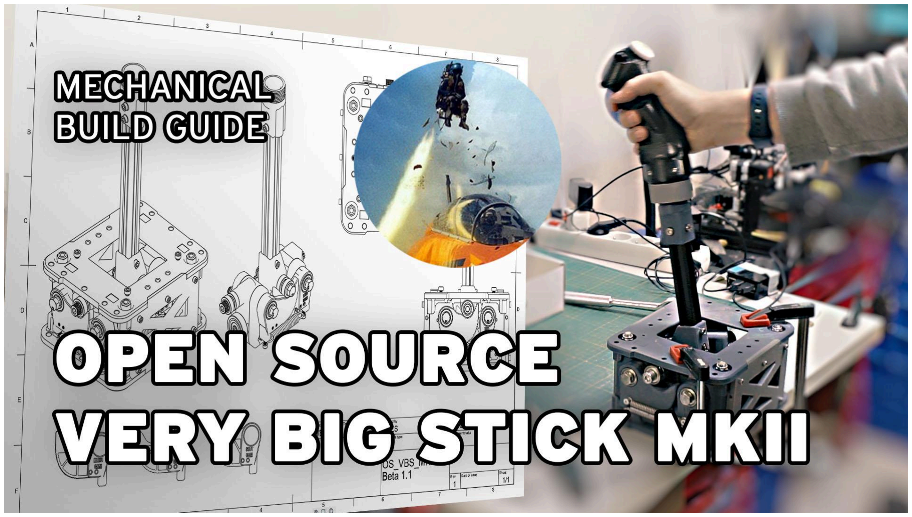
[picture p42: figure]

You can watch the video at this URL: https://www.youtube.com/watch?v=IdYbF5dOYag

## Bill of Materials

This is a live link to a spreadsheet containing the bill of materials for hardware and parts to be printed.

Note that as this time the Electrical section is just a placeholder

Part name | Quantity | Thicker walls required? | grams each | Total grams | Optional?
PitchFrame_TopPlate | 2 | n | 134 | 268
PitchFrame_SidePlate | 2 | n | 47 | 94
TM_M36_2020_Adapter | 1 | y | 31 | 31 | Y
Cam_rollerSpacer | 2 | n | 1 | 2
Cam_bearing_washer | 4 | n | 1 | 4
MainSleeve | 1 | y | 54 | 54
PitchFrame_PillowBlock | 2 | y | 95 | 190
RollFrame_PitchPin_Gear | 1 | y | 43 | 43
RollFrame_PitchPin_Camside | 1 | y | 46 | 46
RollFrame_GearSide | 1 | y | 49 | 49
RollFrame_CamSide | 1 | y | 49 | 49
M12_WasherSpacer | 2 | n | 2 | 4 | Y
SOFT_CAM | 4 | y | 23 | 92
TOTAL Filament PETG | | | | 926 | grams
HARDWARE | | Notes
1KG PETG 1.75mm filament | 1 | PLA+ untested
2020 v slot aluminum rod - Cut to length | 1 | Length depends on your choices
608 bearings | 12
6003 bearings | 4
18x24.7x1 Teflon Washers | 4 | https://www.aliexpress.com/item/4000935512060.html | Y
M3x8mm | 4 | Do nut use countersunk heads
M4x20mm Socket head | 20
M5 vslot drop in nuts | 11
M5x8mm Socket Head | 10 | 6 less if TM adapter is not used
M5x16mm Socket head | 2 | Put into the middle of the camside 6003 bearings for extra strength | Y
M5x50mm | 2 | For the counterweights | Y
M8 washers | 4
M8 Spring Lock washer | 6

M8 Nylon Lock nuts | 8
M8x35mm HEX Head | 3 | Must be hex head for clearance
M8x50mm socket head | 3 | Two of them must be Socket Headed
M8x80mm HEX or Socket Head | 2
M8x100mm HEX head | 4 | HEX head only
M12 Washers | 20 | For counterweights | Y
FRT-C2-301-G1 Rotary damper | 2 | Make sure to get the kind that dampens both directions! | Y
Extension spring with loop ends. ~60mm unloaded | 2 | I used this mcmaster part in the design (3630n293), untested! You'll want to test many springs
Extension spring with loop ends. various lengths | 2 | This is the second set of side springs, try several to tweak | Y
ELECTRICAL (WIP) | | Notes
5pin mini din connector (male) for TM adapter | 1 | https://www.aliexpress.com/item/32859748866.html | y
TLE5010 sensor kit with magnet and PCB | 2 | https://www.aliexpress.com/item/4000549883214.html
Assorted 22 AWG wire in various colours | 1 | get at least a meter worth in several colours.
STM32F103C8 microcontroller | 1 | Be careful to get the exact right version that supports Freejoy, beware of counterfeits
Solder breadboard | 1 | It will be needed to create a "breakout" board for the TLE5010 and Shift register sensors
AS5600 white breakout boards | 2 | This is an alternate to the TLE5010 kit.

## STL Part Reference

Here is information on each stl file included with the build and a reference image showing the correct print orientation.

### PitchFrame_TopPlate.stl (revised 1.4)

Quantity: 2

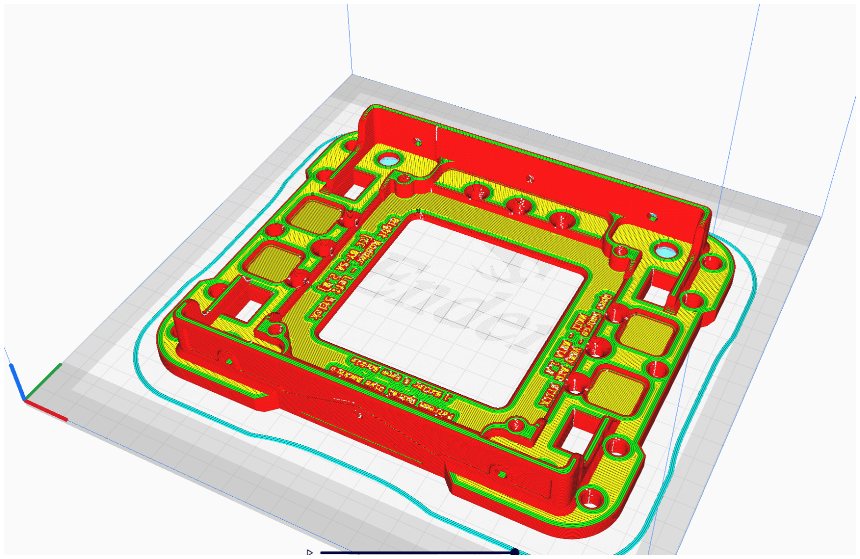
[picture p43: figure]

### PitchFrame_SidePlate.stl

Quantity: 2

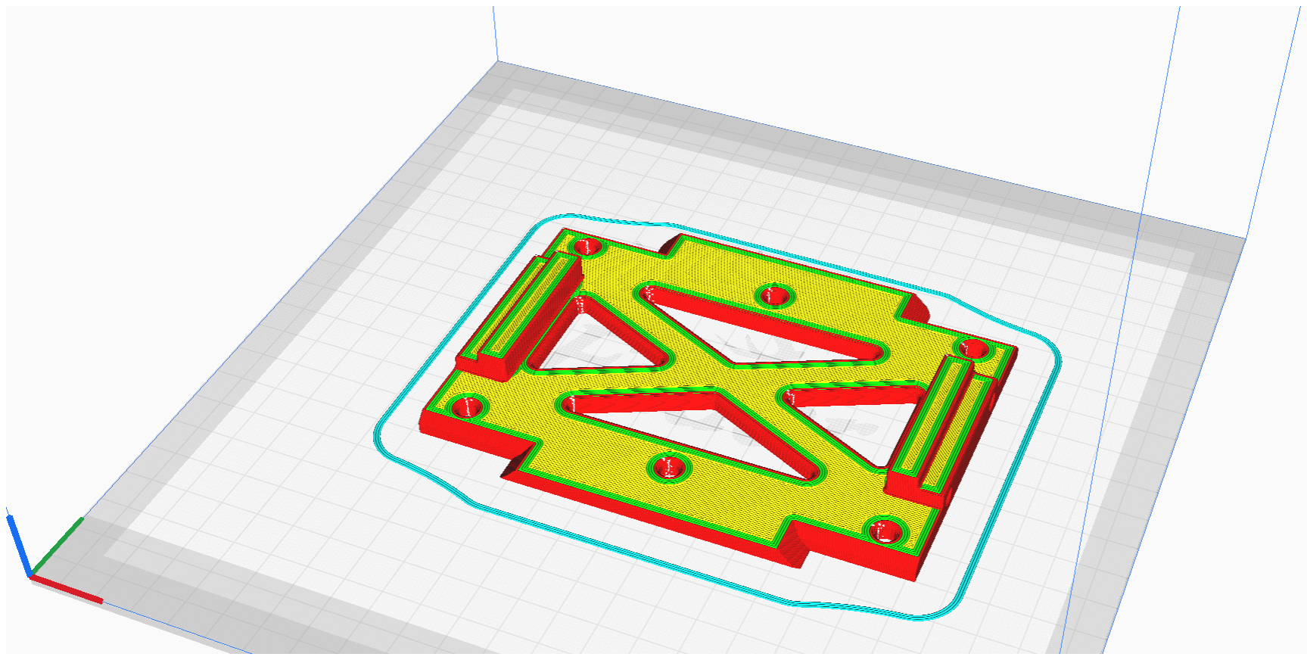
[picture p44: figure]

### TM_M36_2020_Adapter.stl

Quantity: 1

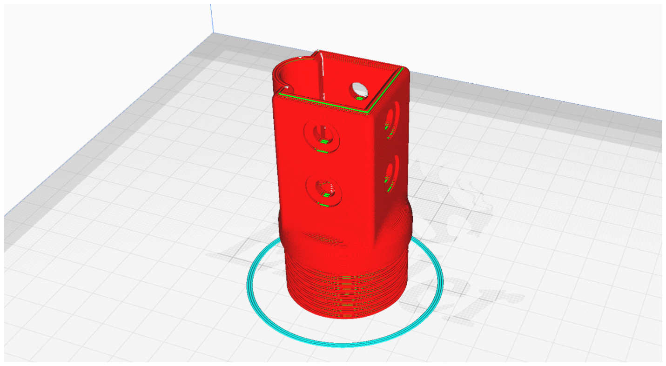
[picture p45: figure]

### Cam_rollerSpacer.stl

Quantity: 2

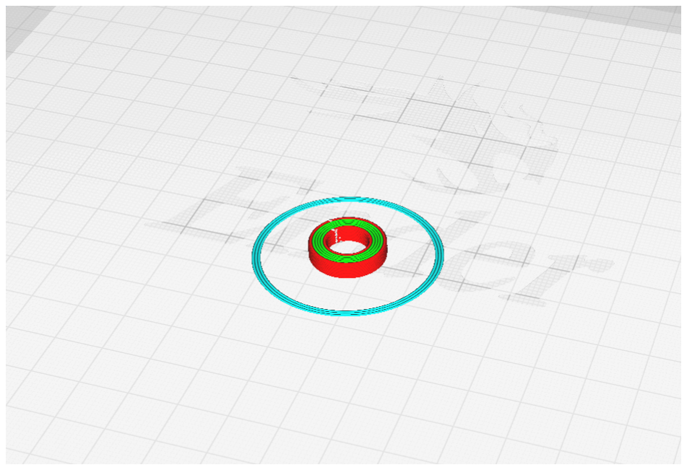
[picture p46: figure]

### Cam_bearing_washer.stl

Quantity: 4

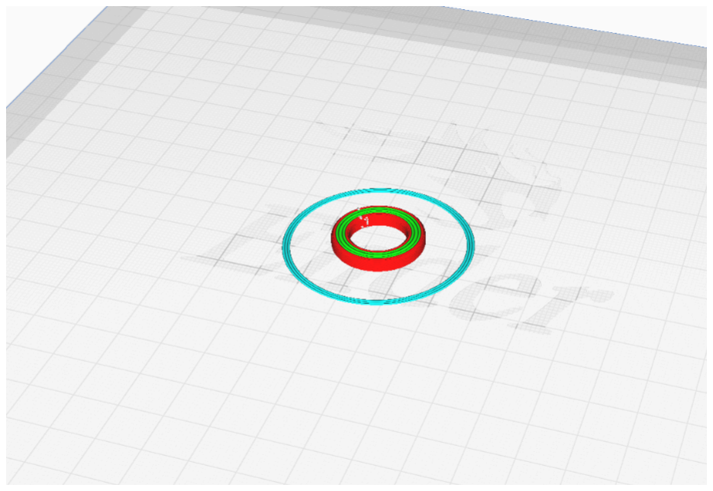
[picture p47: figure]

### MainSleeve.stl (revised 1.4)

Quantity: 1

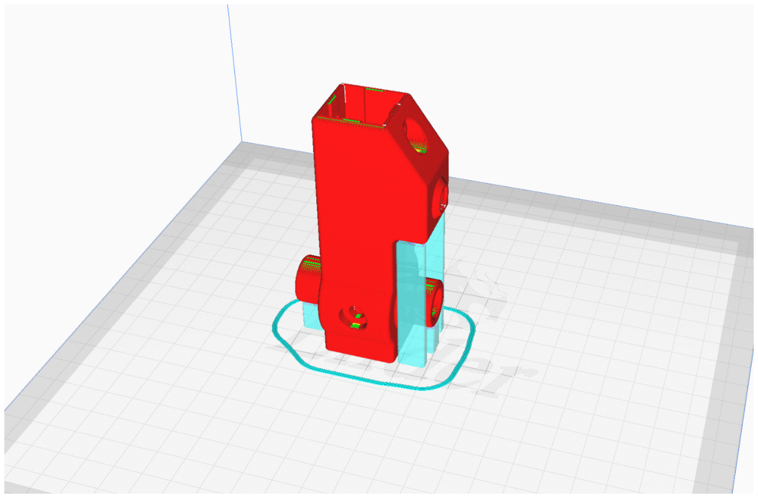
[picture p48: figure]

### PitchFrame_PillowBlock.stl (revised 1.4)

Quantity: 2

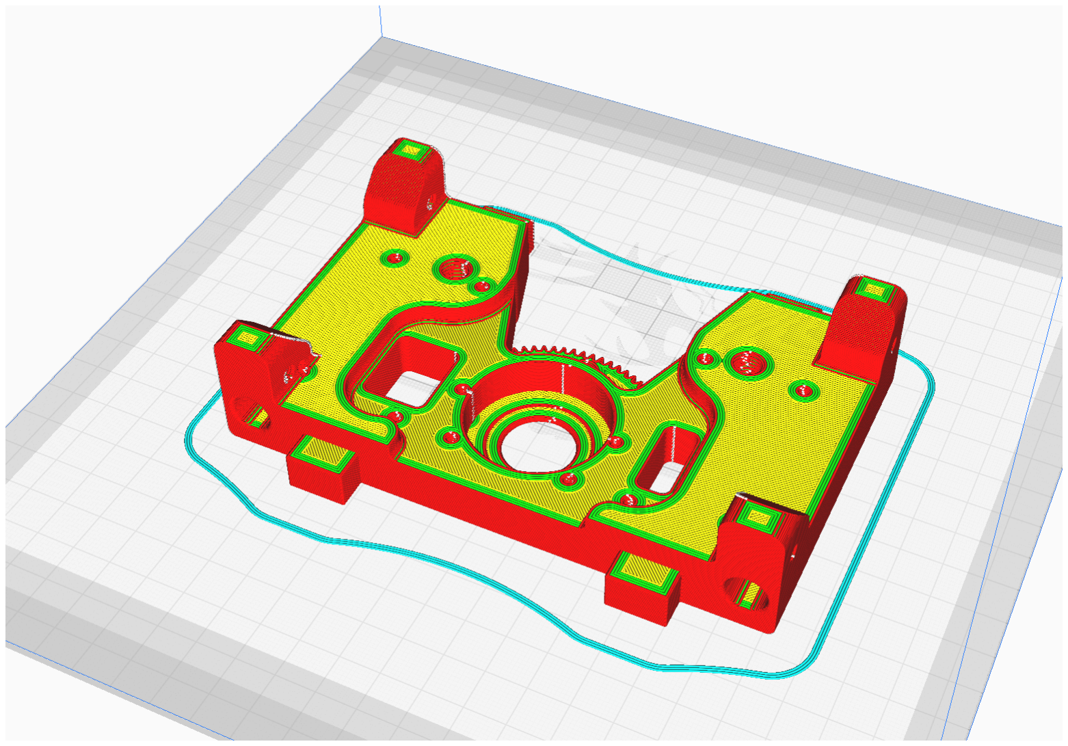
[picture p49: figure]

### RollFrame_PitchPin_Gear.stl (revised 1.4)

Quantity: 1

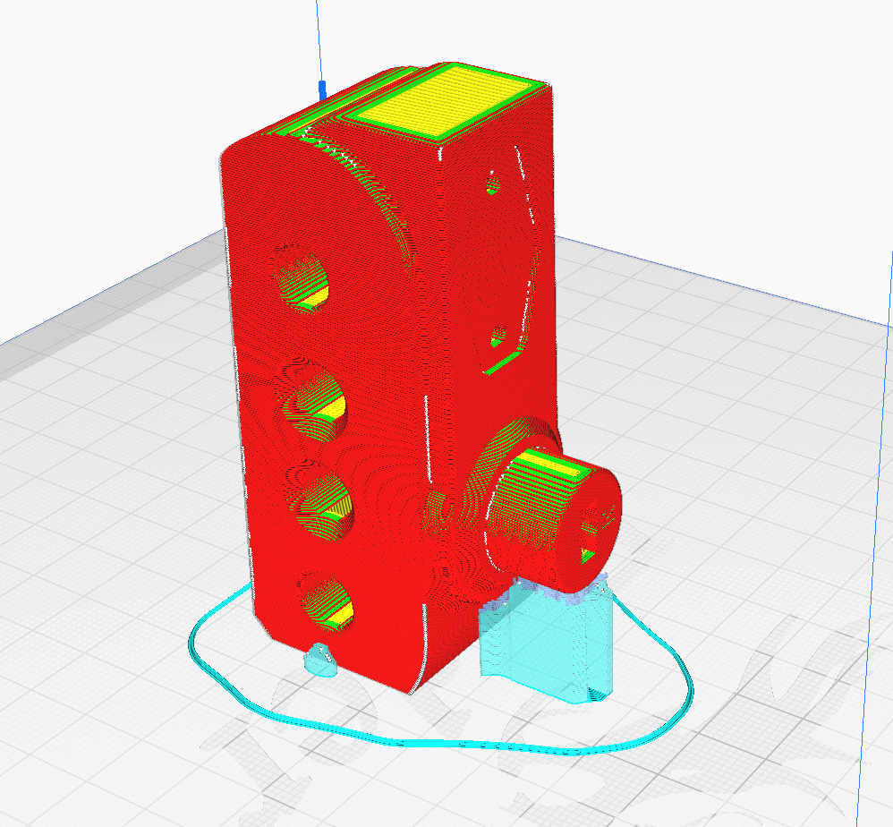
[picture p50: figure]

* Note, this has been revised to print vertically for the magnet slot * Beta 1.4.0

### RollFrame_PitchPin_Camside.stl

Quantity: 1

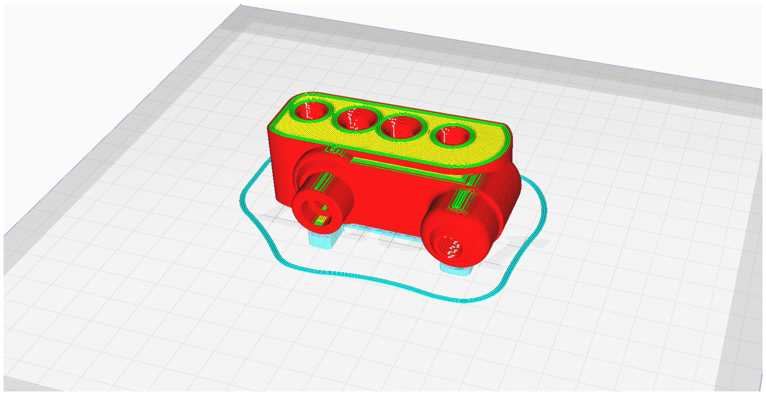
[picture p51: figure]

### RollFrame_GearSide.stl (revised 1.4)

Quantity: 1

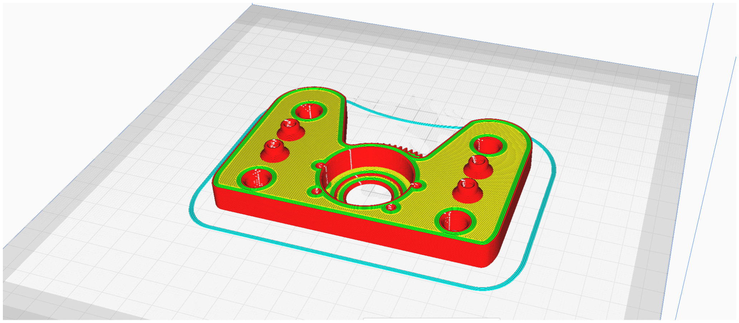
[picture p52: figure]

### RollFrame_CamSide.stl (revised 1.4)

Quantity: 1

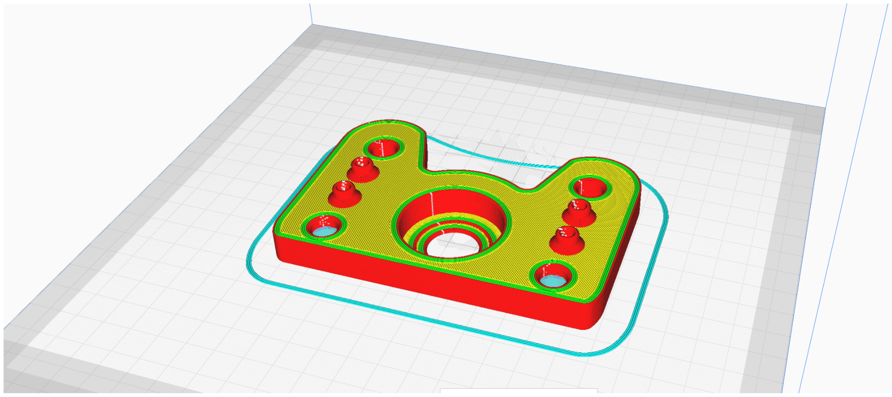
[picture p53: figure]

### M12_WasherSpacer.stl

Quantity: 1
Optional

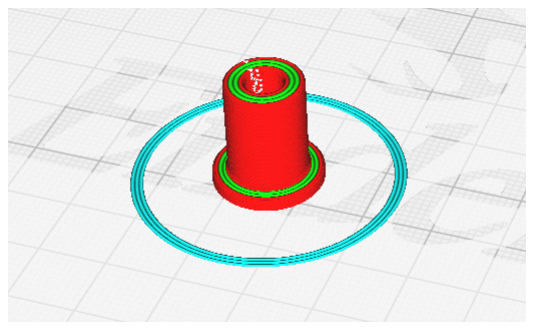
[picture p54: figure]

### AS5600_Sensor_Mount_vr3.stl

Quantity: 2
Optional

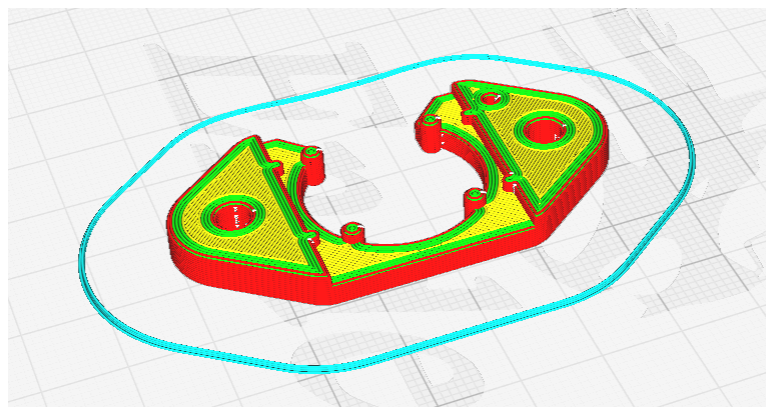
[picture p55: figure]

## CAM Profile Options

The design currently comes with three different options of CAM profiles, They can be mixed and matched on different axis to produce different force feelings, such as a stiffer pitch but a lighter roll motion. They are scaled from Soft to Hard.

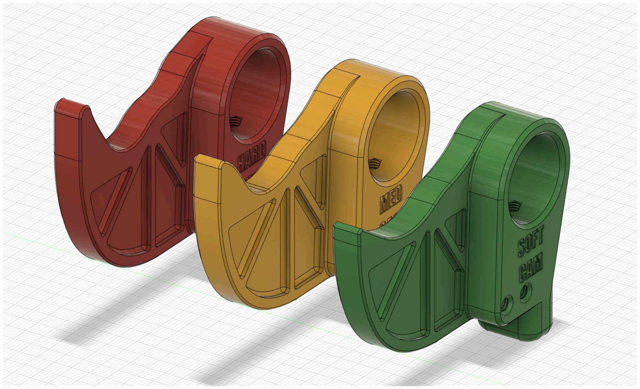
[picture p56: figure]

They also feature mounting for a bottom extension spring as well as 4 M4 holes on the side for mounting a secondary side spring. This can either augment the force of the primary spring or allow the use of a very light spring for low spring force applications like helicopter cyclics.

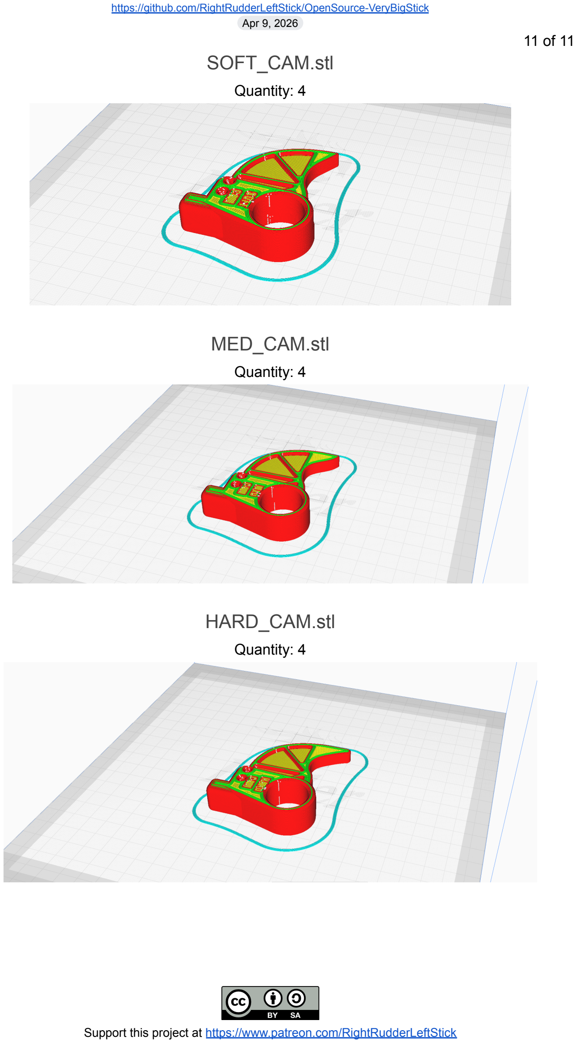
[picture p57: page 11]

### SOFT_CAM.stl

Quantity: 4

### MED_CAM.stl

Quantity: 4

### HARD_CAM.stl

Quantity: 4

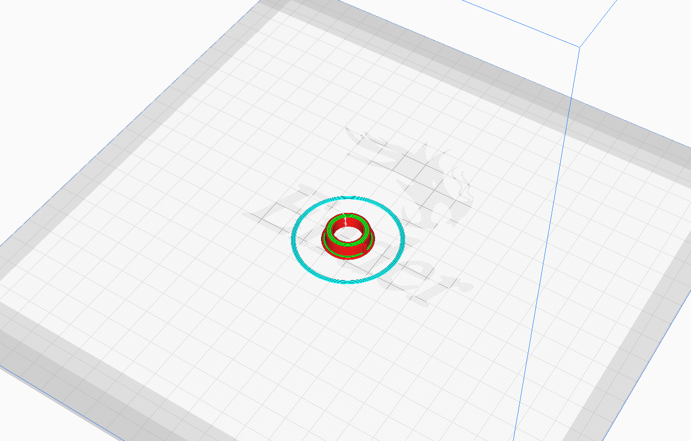
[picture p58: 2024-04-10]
Printable Models/Stick_Base/Images/MINI_DIN_Holder.PNG

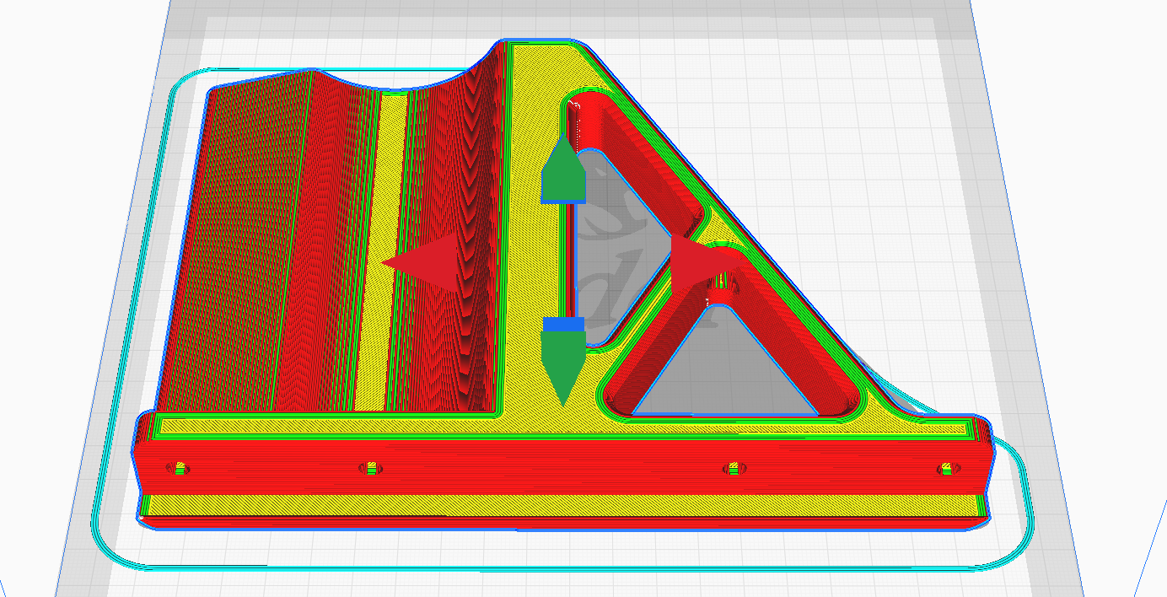
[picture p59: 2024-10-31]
Printable Models/Stick_Base/Images/CHAIR_WHEELCHOCK_Mirror.PNG

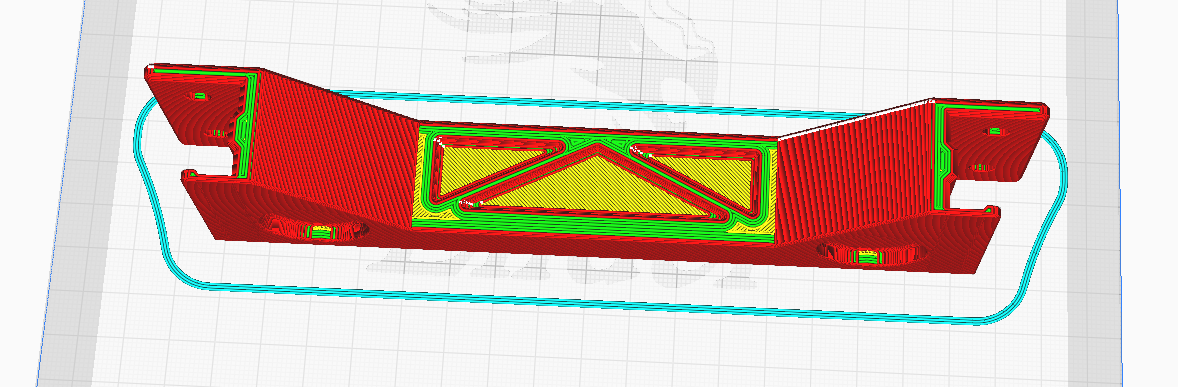
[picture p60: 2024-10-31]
Printable Models/Stick_Base/Images/2020_Crossbar.PNG

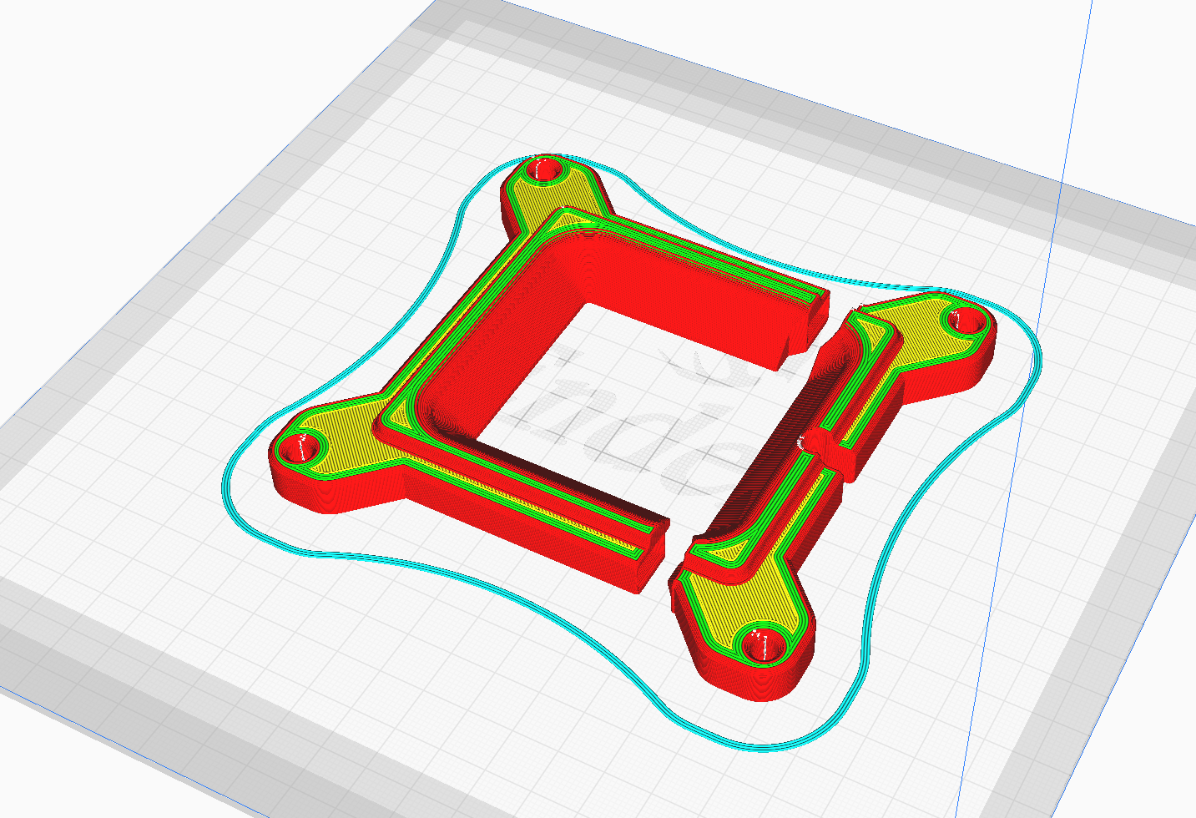
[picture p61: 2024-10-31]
Printable Models/Stick_Base/Images/CYC_Split_RestrictorPlate_20Degrees.PNG

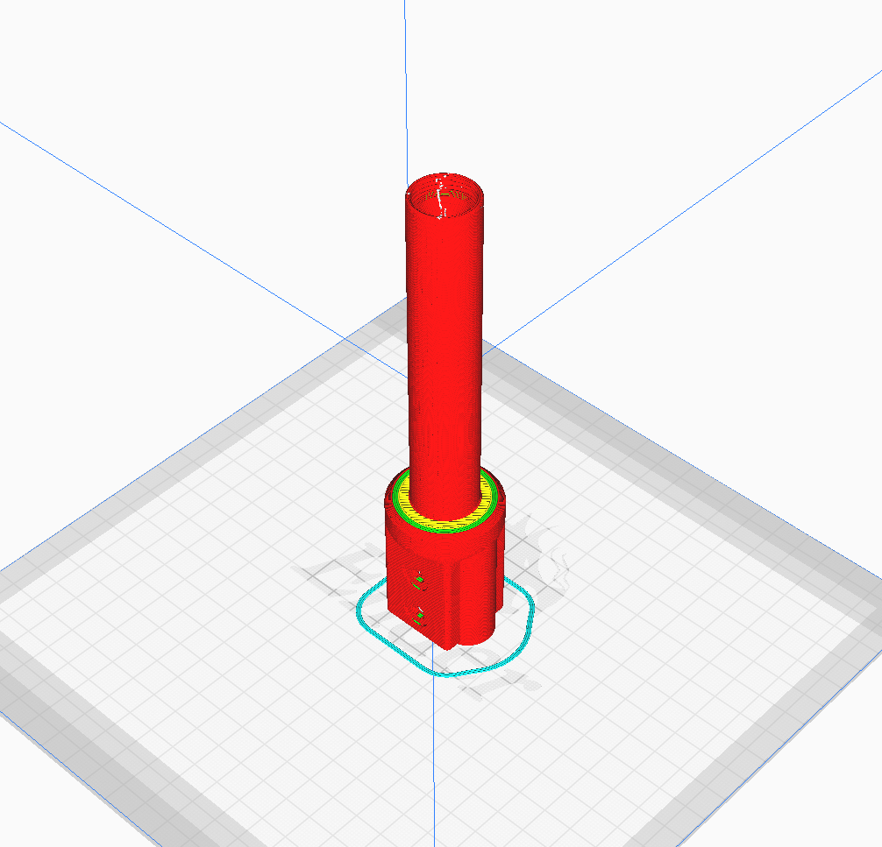
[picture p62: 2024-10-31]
Printable Models/Stick_Base/Images/Bushplane/BushPlane_2020_Grip_Base.PNG

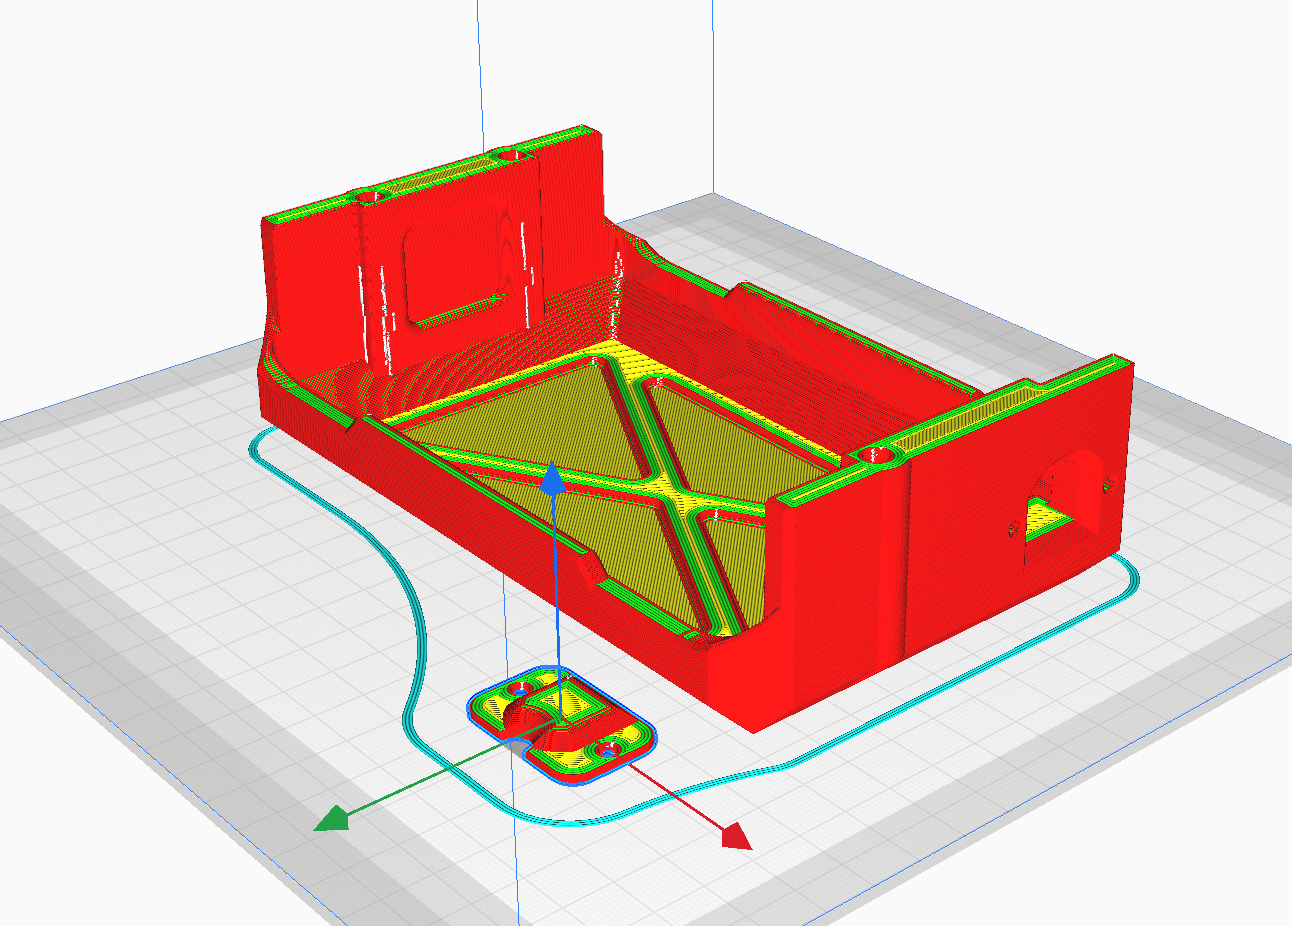
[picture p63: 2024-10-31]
Printable Models/Stick_Base/Images/OuterCamCover_FreejoyUSB.png

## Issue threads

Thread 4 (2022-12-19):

Damper options for axis, geared, square drive or pistons?

RightRudderLeftStick, 2022-12-19:

RightRudderLeftStick, 2022-12-19:
Currently using the authentikit rotorary dampers on gears (since I had a few lying around) which works okay, but time to search and explore other options, maybe things with more resistance or not using gearing and connecting directly to the axis.

Also the damper system is optional in the overall design, as users could run just springs only.

RightRudderLeftStick, 2023-06-17:
went with the FRT-C2-301-G1 as its the easiest to find.

Closed 2023-06-17.

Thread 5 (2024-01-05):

Precision issue when moving stick left or right

freezir12, 2024-01-05:
First: thank you for this design, exactly what i was looking for!
I just assembled all the printed parts and after checking properly i recognized that there is a kinda lot of play on pitch movement. I can move the stick approximately 2 milimeters left and right without resistance before the CAMs start to move. Yaw axis is fine, there is no play.

I have moved each CAM mounting hole in the Pitchframe_Pillowblock 3mm to the outside (77mm distance between center of the holes) in hope this creates a better position of the bearings between the CAMs.

I will print and test tomorrow. I hope i did not increase the distance too much.

(Parts printed in ABS+ on a calibrated printer)

RightRudderLeftStick, 2024-01-06:
Thats odd, the cams should always close up to take up slack.

Is the play in the second stage from the base? It could actually be the holes for the 6003 bearings are oversized and its slopping there.

Could you record a video of it operating?

freezir12, 2024-01-06:
Thx for your quick reply!
The holes for the 6003 bearing is not the cause of that issue. The bearings fit snug, but to be sure i added some tape to make them fit even more tight. The issue still persists.
In attached gif #1 you can see the play of the yaw axis. In comparison you can see how well the pitch axis works in gif #2.
In the attached picture i marked the positioning of bearings and CAMs what i think is the cause of the issue.
I still have black tape around the bearings (i tried to close the gap and make it more tight, do not be confused :) )
Your thoughts are much appreciated! :)

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

RightRudderLeftStick, 2024-01-06:
Thats very odd. Is there anything preventing the dual cams from moving upwards in the neutral position? You are using the medium or hard cams?

freezir12, 2024-01-06:
> Thats very odd. Is there anything preventing the dual cams from moving upwards in the neutral position? You are using the medium or hard cams?
>
> Going to rack my brain on this for awhile, both axis have the same geometry for the roller in relationship to the cams pivot points, so they should behave the same with the same cam profile

I used the medium cams for pitch and yaw.
The cams are pushing upwards against the bearings, i would consider this "neutral position". So no, nothing prevents them from going to neutral position. But from my understandig this is the issue: the cams are pushing upwards against the bearings, but not enough sideways to force the bearings to center.
I checked your Fusion files and realized that the cams pivot point distance is the same for yaw and pitch axis so i was wondering  about the different behaviour too.
I will print the adjusted  Pitchframe_Pillowblock  this evening (should be done by 7pm/8pm and i will let you know if behaviour improved. Thx for your time! :)

RightRudderLeftStick, 2024-01-06:
Looking at the top edge of the two cams, does it look crooked, like the M8x35mm are not perfectly straight? I also am wondering with ABS if there is some dimension that's shrunk, either on the pillowblock or the cams themselves.

freezir12, 2024-01-06:
There is definetly something crooked but very hard to tell right now if it is the cams on the bearings, the screws or the pillow plate. I do not think it is because of shrinkage as all the cams are printed in the same ABS. I guess i will print the pillow plate in PETG after some further research. Going to post updates around 8pm/9pm.

freezir12, 2024-01-07:
Updates:
I found out that the cams did not fit snug with their bearings. That is were the crooked cams came from (pillow plate and screws are fine)
Printing them in PETG did not change anything on the play on the yaw axis movement.
I also printed new cams with their holes put 0.6mm inside (in direction where the roller bearing is). This just removed a little bit of play (0,3mm) but changed the overall behaviour/movement of the cams so i realized this idea is on the wrong path.

The solution for me was to print two stripes in ABS with the following dimensions:
- height: 0,4mm
- wide: 8mm (thickness of the cams)
- length: 40mm  (cutted them to length as i needed it)
Then i used them to put fill the gap (carefully positioning for a perfect fit - no stick wiggle) between cams and roller bearings and melted the stripes on to the cams with acetone (printed new bearings with snug fit in ABS before) as seen on the picture:
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

Then used aceton and sanding paper to make a smooth transition from the cams surface to the stripes. it is not pretty but it works and it saved me filament and printing effort.

RightRudderLeftStick, 2024-01-07:
Was it that the 608 bearings were loose in their sockets or in crooked? The part should be a snug enough fit that they are put in with a rubber mallet or pushing down with a wrench socket.

freezir12, 2024-01-07:
The hole of the cams were to big (i guess as a result of ABS shrinkage, PETG was fine) That made the cams move on the bearings.

RightRudderLeftStick, 2024-01-07:
Ah okay so it was a print issue.

I'm going to mark this issue as closed for now. But definitely post the completed build when you have it!

Also if you haven't printed the top plate note there is a revision with an extra set of M5 holes which are for the damper piston configuration currently under development.

https://www.youtube.com/shorts/R0IVPZbh21o

RightRudderLeftStick, 2024-01-07:
closed

freezir12, 2024-01-07:
Sorry if i re-open by answering but i was not clear enough in my comment:
Having the 603 bearings straight in the cams (very tight fit) did not solve the problem with the movement play on the yaw axis. Adding the stripes to the cams solved the issue for me. I am printing the pillow plate in PETG right now for further testing.

Closed 2024-01-07.

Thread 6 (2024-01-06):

Design TM/VIRPIL M38 thread to 2020 Aluminum Bar adapter

RightRudderLeftStick, 2024-01-06:

RightRudderLeftStick, 2024-01-06:
Seems the current design doesn't leave enough space if you have a PS/2 cable instead of an all custom solution

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

I will keep this STL for people using a chassis DIN connector, but make another one where the thread is offset backwards a bit so the PS/2 cable can go through.

RightRudderLeftStick, 2024-04-10:
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

new 1.3 design with an offset for the cable to fit.

Closed 2024-04-10.

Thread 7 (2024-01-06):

Transition to entirely Freejoy based design

RightRudderLeftStick, 2024-01-06:

RightRudderLeftStick, 2024-01-06:
I have it working with freejoy, but I want to make a breakout PCB design to make setting up electrical much easier.

Need to learn KiCAD and have some prototypes made.

RightRudderLeftStick, 2024-01-07:
Note there is an issue with TM grips and CD4021 that requires a special firmware version, waiting to see if Magners will push it to the main version

RightRudderLeftStick, 2024-04-10:
Actually support freejoy & MMJOY2 (or raw arduino) now.

Closed 2024-04-10.

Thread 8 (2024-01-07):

Work on mounts for the Steering damper for the cyclic mod to attach to the 2020 and the top plate (new revision in 1.2)

RightRudderLeftStick, 2024-01-07:

RightRudderLeftStick, 2024-01-07:
This piece is a bit of a bitch to figure out, especially since my pistons are currently being serviced by a motorcycle mechanic (aliexpress garbage)

Using m8 bolts causes it to slot on the threads, might make an 8mm bushing and use an M5x40 bolt instead.

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

RightRudderLeftStick, 2024-04-10:
This has been moved into a patreon exclusive add-on (gotta pay for 3d printer repairs :( )

Closed 2024-04-10.

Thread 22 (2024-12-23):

Direct Button IO on pcb

edwardker, 2024-12-23:
Hi, love your project!!! I am a noob, could you tell me something more on how to use the extra "Direct_Button_IO" pins on the PCB?
There is also a "no arduino pin" mention on the back? This looks like a supercool board. Would it be compatible with Authentikit? Any plans for a throttle design?

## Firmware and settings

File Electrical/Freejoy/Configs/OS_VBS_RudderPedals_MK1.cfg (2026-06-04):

[DeviceUsbConfig]
FirmwareVersion=1730
DeviceName=OS_RP_MK1
Vid=1420
Pid=2727
USBExchange=5

[PinsConfig]
A0=1
A1=1
A2=1
A3=1
A4=1
A5=5
A6=5
A7=5
A8=1
A9=0
A10=0
A15=0
B0=0
B1=0
B3=0
B4=0
B5=0
B6=0
B7=0
B8=0
B9=0
B10=0
B11=0
B12=1
B13=1
B14=1
B15=1
C13=1
C14=1
C15=1

[ShiftConfig]
Shift0=-1
Shift1=-1
Shift2=-1
Shift3=-1
Shift4=-1

[TimersConfig]
Timer1=50
Timer2=200
Timer3=300
Debounce=50
EncoderPress=30
ButtonsPolling=5
EncodersPolling=1

[ButtonsConfig_0]
ButtonPhysicNumber=7
ButtonType=0
ShiftMod=0
Inverted=0
Disabled=1
DelayTimer=0
PressTimer=0

[ButtonsConfig_1]
ButtonPhysicNumber=4
ButtonType=0
ShiftMod=0
Inverted=0
Disabled=1
DelayTimer=0
PressTimer=0

[ButtonsConfig_2]
ButtonPhysicNumber=3
ButtonType=0
ShiftMod=0
Inverted=0
Disabled=1
DelayTimer=0
PressTimer=0

[ButtonsConfig_3]
ButtonPhysicNumber=2
ButtonType=0
ShiftMod=0
Inverted=0
Disabled=1
DelayTimer=0
PressTimer=0

[ButtonsConfig_4]
ButtonPhysicNumber=1
ButtonType=0
ShiftMod=0
Inverted=0
Disabled=1
DelayTimer=0
PressTimer=0

[ButtonsConfig_5]
ButtonPhysicNumber=0
ButtonType=0
ShiftMod=0
Inverted=0
Disabled=1
DelayTimer=0
PressTimer=0

[ButtonsConfig_6]
ButtonPhysicNumber=11
ButtonType=0
ShiftMod=0
Inverted=0
Disabled=1
DelayTimer=0
PressTimer=0

[ButtonsConfig_7]
ButtonPhysicNumber=10
ButtonType=0
ShiftMod=0
Inverted=0
Disabled=1
DelayTimer=0
PressTimer=0

[ButtonsConfig_8]
ButtonPhysicNumber=9
ButtonType=0
ShiftMod=0
Inverted=0
Disabled=1
DelayTimer=0
PressTimer=0

[ButtonsConfig_9]
ButtonPhysicNumber=8
ButtonType=0
ShiftMod=0
Inverted=0
Disabled=1
DelayTimer=0
PressTimer=0

[ButtonsConfig_10]
ButtonPhysicNumber=12
ButtonType=0
ShiftMod=0
Inverted=0
Disabled=1
DelayTimer=0
PressTimer=0

[ButtonsConfig_11]
ButtonPhysicNumber=12
ButtonType=0
ShiftMod=0
Inverted=0
Disabled=1
DelayTimer=0
PressTimer=0

[ButtonsConfig_12]
ButtonPhysicNumber=12
ButtonType=0
ShiftMod=0
Inverted=0
Disabled=1
DelayTimer=0
PressTimer=0

[ButtonsConfig_13]
ButtonPhysicNumber=12
ButtonType=0
ShiftMod=0
Inverted=0
Disabled=1
DelayTimer=0
PressTimer=0

[ButtonsConfig_14]
ButtonPhysicNumber=12
ButtonType=0
ShiftMod=0
Inverted=0
Disabled=1
DelayTimer=0
PressTimer=0

[ButtonsConfig_15]
ButtonPhysicNumber=12
ButtonType=0
ShiftMod=0
Inverted=0
Disabled=1
DelayTimer=0
PressTimer=0

[ButtonsConfig_16]
ButtonPhysicNumber=12
ButtonType=0
ShiftMod=0
Inverted=0
Disabled=1
DelayTimer=0
PressTimer=0

[ButtonsConfig_17]
ButtonPhysicNumber=12
ButtonType=0
ShiftMod=0
Inverted=0
Disabled=1
DelayTimer=0
PressTimer=0

[ButtonsConfig_18]
ButtonPhysicNumber=6
ButtonType=0
ShiftMod=0
Inverted=0
Disabled=1
DelayTimer=0
PressTimer=0

[ButtonsConfig_19]
ButtonPhysicNumber=12
ButtonType=5
ShiftMod=0
Inverted=0
Disabled=1
DelayTimer=0
PressTimer=0

[ButtonsConfig_20]
ButtonPhysicNumber=12
ButtonType=6
ShiftMod=0
Inverted=0
Disabled=1
DelayTimer=0
PressTimer=0

[ButtonsConfig_21]
ButtonPhysicNumber=12
ButtonType=7
ShiftMod=0
Inverted=0
Disabled=1
DelayTimer=0
PressTimer=0

[ButtonsConfig_22]
ButtonPhysicNumber=12
ButtonType=8
ShiftMod=0
Inverted=0
Disabled=1
DelayTimer=0
PressTimer=0

[ButtonsConfig_23]
ButtonPhysicNumber=-1
ButtonType=0
ShiftMod=0
Inverted=0
Disabled=0
DelayTimer=0
PressTimer=0

[ButtonsConfig_24]
ButtonPhysicNumber=-1
ButtonType=0
ShiftMod=0
Inverted=0
Disabled=0
DelayTimer=0
PressTimer=0

[ButtonsConfig_25]
ButtonPhysicNumber=-1
ButtonType=0
ShiftMod=0
Inverted=0
Disabled=0
DelayTimer=0
PressTimer=0

[ButtonsConfig_26]
ButtonPhysicNumber=-1
ButtonType=0
ShiftMod=0
Inverted=0
Disabled=0
DelayTimer=0
PressTimer=0

[ButtonsConfig_27]
ButtonPhysicNumber=-1
ButtonType=0
ShiftMod=0
Inverted=0
Disabled=0
DelayTimer=0
PressTimer=0

[ButtonsConfig_28]
ButtonPhysicNumber=-1
ButtonType=0
ShiftMod=0
Inverted=0
Disabled=0
DelayTimer=0
PressTimer=0

[ButtonsConfig_29]
ButtonPhysicNumber=-1
ButtonType=0
ShiftMod=0
Inverted=0
Disabled=0
DelayTimer=0
PressTimer=0

[ButtonsConfig_30]
ButtonPhysicNumber=-1
ButtonType=0
ShiftMod=0
Inverted=0
Disabled=0
DelayTimer=0
PressTimer=0

[ButtonsConfig_31]
ButtonPhysicNumber=-1
ButtonType=0
ShiftMod=0
Inverted=0
Disabled=0
DelayTimer=0
PressTimer=0

[ButtonsConfig_32]
ButtonPhysicNumber=-1
ButtonType=0
ShiftMod=0
Inverted=0
Disabled=0
DelayTimer=0
PressTimer=0

[ButtonsConfig_33]
ButtonPhysicNumber=-1
ButtonType=0
ShiftMod=0
Inverted=0
Disabled=0
DelayTimer=0
PressTimer=0

[ButtonsConfig_34]
ButtonPhysicNumber=-1
ButtonType=0
ShiftMod=0
Inverted=0
Disabled=0
DelayTimer=0
PressTimer=0

[ButtonsConfig_35]
ButtonPhysicNumber=-1
ButtonType=0
ShiftMod=0
Inverted=0
Disabled=0
DelayTimer=0
PressTimer=0

[ButtonsConfig_36]
ButtonPhysicNumber=-1
ButtonType=0
ShiftMod=0
Inverted=0
Disabled=0
DelayTimer=0
PressTimer=0

[ButtonsConfig_37]
ButtonPhysicNumber=-1
ButtonType=0
ShiftMod=0
Inverted=0
Disabled=0
DelayTimer=0
PressTimer=0

[ButtonsConfig_38]
ButtonPhysicNumber=-1
ButtonType=0
ShiftMod=0
Inverted=0
Disabled=0
DelayTimer=0
PressTimer=0

[ButtonsConfig_39]
ButtonPhysicNumber=-1
ButtonType=0
ShiftMod=0
Inverted=0
Disabled=0
DelayTimer=0
PressTimer=0
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

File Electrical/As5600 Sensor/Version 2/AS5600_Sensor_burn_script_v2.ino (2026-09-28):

#include <Wire.h>

// ============================================================
// STM32 BLUE PILL AS5600 PROGRAMMER / BURNER
// ============================================================
//
// Purpose:
// Permanently program an AS5600 with:
//
//     ZPOS = 2787  (~245 degrees)
//     MPOS = 3356  (~295 degrees)
//
// The same firmware automatically detects the AS5600 on either:
//
//     I2C1: PB6 = SCL, PB7 = SDA
//     I2C2: PB10 = SCL, PB11 = SDA
//
// No magnet is required during programming.
//
// PA1:
//     Normally left floating/high.
//     Connect PA1 to GND to trigger the permanent burn.
//
// PC13:
//     Onboard Blue Pill LED, active LOW.
//
// Wiring:
//
// BLUE PILL       AS5600
// ---------       ------
// 3.3V     ->     VCC
// GND      ->     GND
//
// I2C1:
// PB6      ->     SCL
// PB7      ->     SDA
//
// OR
//
// I2C2:
// PB10     ->     SCL
// PB11     ->     SDA
//
// ============================================================


// ------------------------------------------------------------
// AS5600
// ------------------------------------------------------------

const uint8_t AS5600_ADDR = 0x36;


// ------------------------------------------------------------
// Pins
// ------------------------------------------------------------

const uint8_t BURN_PIN = PA1;
const uint8_t LED_PIN  = PC13;


// ------------------------------------------------------------
// HARD-CODED ANGLE RANGE
// ------------------------------------------------------------

const uint16_t START_VAL = 2787;
const uint16_t END_VAL   = 3356;


// ------------------------------------------------------------
// AS5600 REGISTERS
// ------------------------------------------------------------

const uint8_t REG_STATUS  = 0x0B;
const uint8_t REG_ANGLE   = 0x0C;
const uint8_t REG_RAW     = 0x0E;

const uint8_t REG_ZPOS    = 0x01;
const uint8_t REG_MPOS    = 0x03;

const uint8_t REG_BURN    = 0xFF;

const uint8_t BURN_ANGLE  = 0x80;


// ------------------------------------------------------------
// STATUS REGISTER
//
// STATUS bit 5 = MD
// MD = Magnet Detected
//
// We use this ONLY to suppress useless angle printing.
// It does NOT prevent programming or burning.
// ------------------------------------------------------------

const uint8_t STATUS_MD = 0x20;


// ------------------------------------------------------------
// I2C buses
//
// STM32duino TwoWire constructor:
// TwoWire(SDA, SCL)
// ------------------------------------------------------------

TwoWire Wire1(PB7, PB6);
TwoWire Wire2(PB11, PB10);


// Pointer to whichever bus contains the AS5600
TwoWire* AS5600_Wire = nullptr;


// ------------------------------------------------------------
// Timing
// ------------------------------------------------------------

unsigned long lastPrint = 0;


// ============================================================
// READ 8-BIT REGISTER
// ============================================================

bool readReg8(uint8_t reg, uint8_t &value)
{
  if (AS5600_Wire == nullptr)
    return false;

  AS5600_Wire->beginTransmission(AS5600_ADDR);
  AS5600_Wire->write(reg);

  if (AS5600_Wire->endTransmission(false) != 0)
    return false;

  uint8_t count = AS5600_Wire->requestFrom(AS5600_ADDR, (uint8_t)1);

  if (count != 1)
    return false;

  value = AS5600_Wire->read();

  return true;
}


// ============================================================
// READ 16-BIT REGISTER
//
// AS5600 registers are 12-bit values stored as:
//
//     HIGH BYTE
//     LOW BYTE
//
// Only the lower 12 bits are used.
// ============================================================

bool readReg16(uint8_t reg, uint16_t &value)
{
  if (AS5600_Wire == nullptr)
    return false;

  AS5600_Wire->beginTransmission(AS5600_ADDR);
  AS5600_Wire->write(reg);

  if (AS5600_Wire->endTransmission(false) != 0)
    return false;

  uint8_t count = AS5600_Wire->requestFrom(AS5600_ADDR, (uint8_t)2);

  if (count != 2)
    return false;

  uint8_t highByte = AS5600_Wire->read();
  uint8_t lowByte  = AS5600_Wire->read();

  value = ((uint16_t)highByte << 8) | lowByte;

  value &= 0x0FFF;

  return true;
}


// ============================================================
// WRITE 16-BIT REGISTER
// ============================================================

bool writeReg16(uint8_t reg, uint16_t value)
{
  if (AS5600_Wire == nullptr)
    return false;

  value &= 0x0FFF;

  AS5600_Wire->beginTransmission(AS5600_ADDR);

  AS5600_Wire->write(reg);

  // High byte
  AS5600_Wire->write((value >> 8) & 0x0F);

  // Low byte
  AS5600_Wire->write(value & 0xFF);

  uint8_t error = AS5600_Wire->endTransmission();

  if (error != 0)
    return false;

  // Give AS5600 time to process the write
  delay(5);

  return true;
}


// ============================================================
// DETECT AS5600 ON A BUS
//
// We don't require a magnet.
//
// We simply attempt to read a valid register.
// ============================================================

bool detectAS5600(TwoWire &bus)
{
  bus.begin();
  bus.setClock(400000);

  bus.beginTransmission(AS5600_ADDR);

  if (bus.endTransmission() != 0)
    return false;

  // Make sure we can actually read from the device.
  bus.beginTransmission(AS5600_ADDR);
  bus.write(REG_RAW);

  if (bus.endTransmission(false) != 0)
    return false;

  uint8_t count = bus.requestFrom(AS5600_ADDR, (uint8_t)2);

  if (count != 2)
    return false;

  bus.read();
  bus.read();

  return true;
}


// ============================================================
// FIND AS5600
//
// First try I2C1.
// Then try I2C2.
// ============================================================

bool findAS5600()
{
  Serial.println();
  Serial.println(F("Searching for AS5600..."));

  Serial.println(F("Checking I2C1: PB6=SCL, PB7=SDA"));

  if (detectAS5600(Wire1))
  {
    AS5600_Wire = &Wire1;

    Serial.println(F("AS5600 FOUND on I2C1."));
    return true;
  }

  Serial.println(F("Not found on I2C1."));

  Serial.println(F("Checking I2C2: PB10=SCL, PB11=SDA"));

  if (detectAS5600(Wire2))
  {
    AS5600_Wire = &Wire2;

    Serial.println(F("AS5600 FOUND on I2C2."));
    return true;
  }

  Serial.println(F("AS5600 NOT FOUND."));

  return false;
}


// ============================================================
// SHOW ANGLE
//
// IMPORTANT:
//
// If there is no magnet, nothing is printed.
//
// This is purely informational and has NO effect on burning.
// ============================================================

void printAngleIfMagnetPresent()
{
  if (millis() - lastPrint < 500)
    return;

  lastPrint = millis();

  uint8_t status;

  if (!readReg8(REG_STATUS, status))
    return;

  // No magnet -> don't print angle
  if (!(status & STATUS_MD))
    return;

  uint16_t rawAngle;

  if (!readReg16(REG_RAW, rawAngle))
    return;

  rawAngle &= 0x0FFF;

  Serial.print(F("Magnet detected - Raw angle: "));
  Serial.println(rawAngle);
}


// ============================================================
// WRITE AND VERIFY ZPOS / MPOS
// ============================================================

bool programAngleRange()
{
  Serial.println();
  Serial.println(F("========================================"));
  Serial.println(F("PROGRAMMING AS5600"));
  Serial.println(F("========================================"));

  Serial.print(F("ZPOS = "));
  Serial.println(START_VAL);

  Serial.print(F("MPOS = "));
  Serial.println(END_VAL);

  Serial.println();

  // ----------------------------------------------------------
  // Write ZPOS
  // ----------------------------------------------------------

  Serial.println(F("Writing ZPOS..."));

  if (!writeReg16(REG_ZPOS, START_VAL))
  {
    Serial.println(F("ERROR: ZPOS write failed."));
    return false;
  }

  Serial.println(F("ZPOS write OK."));


  // ----------------------------------------------------------
  // Write MPOS
  // ----------------------------------------------------------

  Serial.println(F("Writing MPOS..."));

  if (!writeReg16(REG_MPOS, END_VAL))
  {
    Serial.println(F("ERROR: MPOS write failed."));
    return false;
  }

  Serial.println(F("MPOS write OK."));


  // ----------------------------------------------------------
  // Read back ZPOS
  // ----------------------------------------------------------

  uint16_t zposRead;

  if (!readReg16(REG_ZPOS, zposRead))
  {
    Serial.println(F("ERROR: Could not read ZPOS back."));
    return false;
  }

  Serial.print(F("ZPOS readback = "));
  Serial.println(zposRead);

  if (zposRead != START_VAL)
  {
    Serial.println(F("ERROR: ZPOS verification FAILED."));
    return false;
  }


  // ----------------------------------------------------------
  // Read back MPOS
  // ----------------------------------------------------------

  uint16_t mposRead;

  if (!readReg16(REG_MPOS, mposRead))
  {
    Serial.println(F("ERROR: Could not read MPOS back."));
    return false;
  }

  Serial.print(F("MPOS readback = "));
  Serial.println(mposRead);

  if (mposRead != END_VAL)
  {
    Serial.println(F("ERROR: MPOS verification FAILED."));
    return false;
  }


  Serial.println();
  Serial.println(F("ZPOS verification OK."));
  Serial.println(F("MPOS verification OK."));
  Serial.println(F("RAM values are correct."));

  return true;
}


// ============================================================
// WAIT FOR PA1 TO BE GROUNDED
// ============================================================

void waitForBurnTrigger()
{
  Serial.println();
  Serial.println(F("----------------------------------------"));
  Serial.println(F("READY TO BURN"));
  Serial.println(F("----------------------------------------"));
  Serial.println(F("Connect PA1 to GND to permanently burn."));
  Serial.println(F("Magnet is NOT required."));
  Serial.println();

  // Wait until PA1 is grounded.
  while (digitalRead(BURN_PIN) == HIGH)
  {
    printAngleIfMagnetPresent();
    delay(10);
  }

  // Require PA1 to remain LOW briefly.
  delay(100);

  // Confirm it is still grounded.
  if (digitalRead(BURN_PIN) == LOW)
  {
    Serial.println();
    Serial.println(F("BURN TRIGGER DETECTED."));
  }
}


// ============================================================
// PERFORM OTP BURN
// ============================================================

bool burnAngle()
{
  Serial.println();
  Serial.println(F("========================================"));
  Serial.println(F("SENDING BURN_ANGLE COMMAND"));
  Serial.println(F("========================================"));

  Serial.println(F("Writing 0x80 to register 0xFF..."));

  AS5600_Wire->beginTransmission(AS5600_ADDR);

  AS5600_Wire->write(REG_BURN);
  AS5600_Wire->write(BURN_ANGLE);

  uint8_t error = AS5600_Wire->endTransmission();

  if (error != 0)
  {
    Serial.print(F("ERROR: Burn command I2C error = "));
    Serial.println(error);

    return false;
  }

  delay(10);

  Serial.println(F("BURN_ANGLE command sent."));
  Serial.println(F("The AS5600 OTP programming operation has been requested."));

  return true;
}


// ============================================================
// SETUP
// ============================================================

void setup()
{
  // LED
  pinMode(LED_PIN, OUTPUT);

  // LED OFF
  digitalWrite(LED_PIN, HIGH);


  // PA1 uses internal pull-up.
  //
  // Normally:
  //     PA1 = HIGH
  //
  // Burn:
  //     PA1 -> GND
  //
  pinMode(BURN_PIN, INPUT_PULLUP);


  // Serial
  Serial.begin(115200);

  delay(1000);

  Serial.println();
  Serial.println(F("========================================"));
  Serial.println(F("STM32 AS5600 PROGRAMMER"));
  Serial.println(F("========================================"));

  Serial.print(F("Target ZPOS: "));
  Serial.println(START_VAL);

  Serial.print(F("Target MPOS: "));
  Serial.println(END_VAL);

  Serial.println();
  Serial.println(F("Magnet is NOT required."));
  Serial.println(F("Angle output is suppressed when no magnet"));
  Serial.println(F("is detected."));
  Serial.println();


  // ----------------------------------------------------------
  // Find AS5600
  // ----------------------------------------------------------

  if (!findAS5600())
  {
    Serial.println();
    Serial.println(F("STOPPED."));
    Serial.println(F("Check VCC, GND, SDA and SCL."));

    // Fast blink = no AS5600 found
    while (true)
    {
      digitalWrite(LED_PIN, LOW);
      delay(150);
      digitalWrite(LED_PIN, HIGH);
      delay(150);
    }
  }


  // ----------------------------------------------------------
  // AS5600 detected
  // ----------------------------------------------------------

  digitalWrite(LED_PIN, LOW);

  Serial.println();
  Serial.println(F("AS5600 communication established."));


  // ----------------------------------------------------------
  // Program ZPOS / MPOS
  // ----------------------------------------------------------

  if (!programAngleRange())
  {
    Serial.println();
    Serial.println(F("PROGRAMMING FAILED."));
    Serial.println(F("OTP burn has NOT been attempted."));

    // Error indication
    while (true)
    {
      digitalWrite(LED_PIN, LOW);
      delay(500);
      digitalWrite(LED_PIN, HIGH);
      delay(500);
    }
  }


  // ----------------------------------------------------------
  // Wait for physical burn trigger
  // ----------------------------------------------------------

  waitForBurnTrigger();


  // ----------------------------------------------------------
  // Burn
  // ----------------------------------------------------------

  if (burnAngle())
  {
    Serial.println();
    Serial.println(F("========================================"));
    Serial.println(F("BURN COMMAND COMPLETE"));
    Serial.println(F("========================================"));
    Serial.println(F("Remove PA1 from GND."));
    Serial.println(F("Programming sequence finished."));
  }
  else
  {
    Serial.println();
    Serial.println(F("BURN COMMAND FAILED."));
  }


  // Turn LED off when finished
  digitalWrite(LED_PIN, HIGH);

  // Stop here.
  while (true)
  {
    delay(1000);
  }
}


// ============================================================
// LOOP
// ============================================================

void loop()
{
  // Everything is handled in setup().
  // Nothing further is required.
}

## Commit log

2022-01-12 STEP file for January 2022-01-11
    Still need to add sensor system, and maybe geared dampers?
    [Object 77-B BIG v34_2022-1-11.step]
2022-01-13 new revision with more rigid box design.
    Uses self tapping wood screws to hold the box together
2022-01-14 Add files via upload
    new slot box, nice and rigid! uses a ton of filament though
2022-01-22 latest revision. Got space for rotary dampers to use on each axis. still to be done is the hall effect sensor mounts
2022-01-22 adjusted bottom clearance and rised cam axis back up 3mm
2022-12-19 uploaded the current F3D file
2023-06-18 Beta 1.1 public release
    [Cam_bearing_washer.3mf, Cam_rollerSpacer.3mf, HARD CAM.3mf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]
2023-10-24 new TM adapters with cutouts for the bottom X
    [TM_M36_2020_Adapter.3mf]
2023-12-28 revised to beta 1.2 with a new Pitchframe_PillowBlock and PitchFrame_TopPlate which will be required for the cyclic damper mod going forward
    [PitchFrame_PillowBlock.3mf, PitchFrame_TopPlate.3mf]
2024-04-06 beta 1.3 preview
    [ASSY_USBCABLE_STRAIN_RELIEF.3mf, Cyclic_RestrictorPlate_20degrees.3mf, HARD CAM.3mf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]
2024-04-07 placeholder PCBWAY links
2024-04-07 changed the STL folder to printable models since they are actually 3mf files
    [ASSY_USBCABLE_STRAIN_RELIEF.3mf, Cam_bearing_washer.3mf, Cam_rollerSpacer.3mf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]
2024-04-07 added the step file for 1.3
    [2020_Crossbar.3mf, CHAIR_WHEELCHOCK.3mf, CHAIR_WHEELCHOCK_Mirror.3mf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]
2024-04-09 Update README.md
    updated the pcbway links
2024-04-09 added the electrical thumbnail
    [2020_CYC_OFFSET.3mf]
2024-04-10 Update README.md
    added referral URL for pcbway
2024-04-10 new build guide pdf
    [2020_CYC_OFFSET.3mf, Cam_bearing_washer.3mf, MED_CAM.3mf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]
2024-04-15 added the community folder
    [McDinggle_TM_Adapter_short.stl, McDinggle_VKB_Adapter.stl]
2024-04-15 added a guide for what cams to print with an image. Also reorganized the git to put the images out of the root
2024-04-15 Update README.md
    MINI DIN PCB FOOTPRINT IS WRONG
2024-04-15 fixed the breakout board with revision 1.4
2024-05-12 added a w.i.p of the freejoy stuff
    [OSVBS_TMGRIP_v5.cfg]
2024-07-05 added the restrictor plate and bushplane grip
    [BushPlane_12mm_ButtonCap.3mf, Bushplane_2020_Grip_Base.3mf, CYC_Split_RestrictorPlate_20degrees.3mf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]
2024-07-05 added the spade grip adapter
    [SidePlate_Cover.3mf]
2024-07-05 forgot the stl lol
    [SpitfireSpade_MountBracket.3mf]
2024-07-05 added the wheel chocks and crossbar updates
    [2020_Crossbar.3mf, CHAIR_WHEELCHOCK.3mf, CHAIR_WHEELCHOCK_Mirror.3mf]
2024-07-05 added the side cover with the usb-b port hole
    [OuterCamCover_FreejoyUSB.3mf]
2024-07-19 breakout board had an short on BTN4 and BTN14 revised breakout to 1.5. I had to reorder the BTN order to make it route
2024-07-30 updated the version number on the pitchframe_topplate.3mf
    [PitchFrame_TopPlate.3mf]
2024-07-30 changed the branding font on OuterCamCover_Solid.3mf to match the rest of the new branding
    [OuterCamCover_Solid.3mf]
2025-12-18 new TPU boot for going over the top of the gimbal as a dust cover.
    [TPU_BOOT.3mf]
2025-12-19 added the TPU boot for the gimbal
    [TPU_BOOT.3mf]
2025-12-22 changed all the 3mf files to STLs as there is wierd behaviour on the cura generated ones in bambu-orcaslicer:
    [2020_CYC_OFFSET.3mf, 2020_CYC_OFFSET.stl, 2020_Crossbar.3mf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]
2025-12-22 forgot to convert the bushplane grip 3mf to stls
    [2020_Crossbar.stl, BushPlane_12mm_ButtonCap.3mf, BushPlane_12mm_ButtonCap.stl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]
2025-12-28 added bill of materials image
2025-12-29 added the release 1.0 of the pedals to the printable files
    [2020_WIRE_RELIEF.stl, BarSleeve_Magnet.stl, Base_FrontYoke.stl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]
2026-04-09 added the first draft of the script to make the STM32 burn the AS5600 sensor over i2c
2026-04-09 version 1.4.0 updated files
    [AS5600_Sensor_Mount_vr3.stl]
2026-04-09 Deleted _obsolete, added the version 1.4 step file
    [Cam_bearing_washer.3mf, Cyclic_RestrictorPlate_20degrees.3mf, TM_M36_2020_Adapter.3mf]
2026-04-09 flathead magnet image for the electrical readme
2026-04-09 Update electrical README.md
    How to setup the AS5600 sensor
2026-04-09 Update README.md
    Changed B6 to B10 and B7 to B11 to match the freejoy configurator pin labels
2026-04-10 Added config files for mmjoy and freejoy for the pedals
    [OS_VBS_RudderPedals_MK1.cfg]
2026-05-22 updated the patreon tier info on the stl, added the missing mirrored toebrake spring parts
    [Pedal_GearBase_frame.stl, ToeBrake_SpringBracket(mirror).stl, Toebrake_SpringARm(mirror).stl]
2026-05-22 duplicated the as5600 bracket into the pedal stl folder as well
    [AS5600_Sensor_Mount_vr3.stl]
2026-05-22 reorganized the pedal files into sub directories, organized the BOM into sub modules
    [2020_WIRE_RELIEF.stl, AS5600_Sensor_Mount_vr3.stl, BarSleeve_CamRoller.stl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]
2026-05-31 Rear_WallStiffenBar(Mirror).stl wasn't mirrored, just rotated.
    [Rear_WallStiffenBar(Mirror).stl]
